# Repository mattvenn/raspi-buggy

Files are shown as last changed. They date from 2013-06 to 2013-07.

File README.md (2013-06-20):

# Raspberry pi scratch controlled drawing buggy

Simple buggy to control with scratch and python.

## Scratch 

A python listener is run on the raspberry pi which uses scratch's mesh networking capability to turn commands from scratch into motor controls.

Scratch itself is run on another computer to avoid the large overhead of sending graphics over the network.

## Python

The buggy can also be controlled direct from python.

# Build instructions

See the [instructions](docs/instructions.md) here.

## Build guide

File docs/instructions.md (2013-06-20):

# Buggy build instructions

# Get the parts

You will need:

*  some [male to male wires](http://oomlout.co.uk/products/jumper-wires-70-piece)
*  some [female to male wires](http://oomlout.co.uk/products/premium-female-to-female-jumper-wires-x21)
*  [l293d motor driver](http://oomlout.co.uk/products/motor-controller-l293d)
*  [400 point breadboard](http://oomlout.co.uk/collections/prototyping/products/breadboard-400-point)
*  4 AA battery holder and 4 *rechargable batteries* *TODO*
*  [buggy unit](http://www.mindsetsonline.co.uk/product_info.php?cPath=17_134_685&products_id=1034)
*  pen and bluetack if you want to do some drawing.

# Tools required

* flat screwdriver
* pliers
* soldering iron? *TODO*

# Build the buggy

Follow the instructions that came with the buggy, but don't put the wires through the central hole. Also, don't connect the switches to the motors. We'll use the l293d chip to control the motors instead.

# Build the circuit

Follow this diagram to build the circuit, but don't insert the batteries yet. The most important parts to get right are:

*  The black and red connections from the battery holder need to be the right way round.
*  The l293d chip needs to be the right way round - the little notch should be on the right.

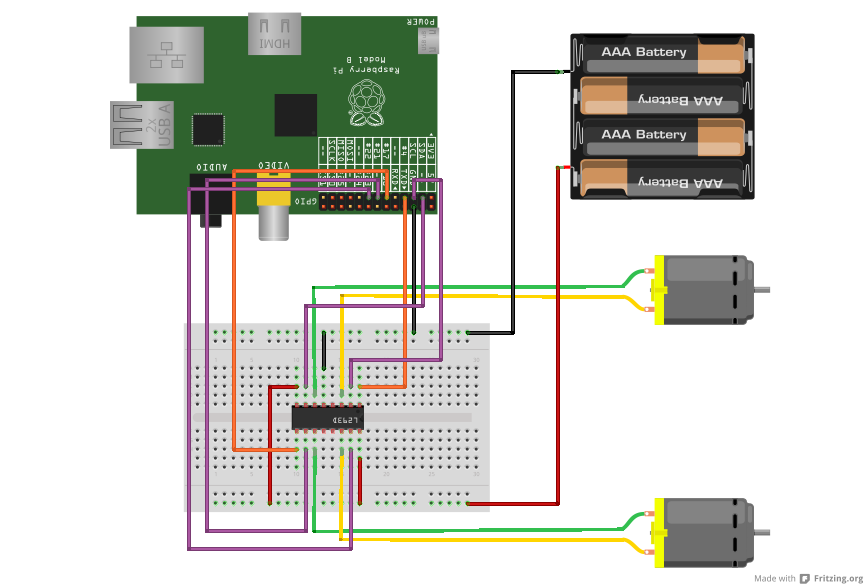
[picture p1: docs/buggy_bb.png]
circuit


The l293d is the chip that amplifies the small current from the raspberry pi to the larger current we need to drive the motors. It also lets us drive the motors forwards and backwards. You can learn more about the [l293d here.](http://www.ti.com/lit/ds/symlink/l293d.pdf)

# Setup the software on the Raspberry pi

## Log in to the raspberry pi

*TODO*
You will need to power up the raspberry pi and connect to it over the network.

## Download the buggy software

On the raspberry pi, start a terminal. Then run these commands to download the software:

    wget https://github.com/mattvenn/raspi-buggy/archive/master.zip
    unzip master.zip

Then we need to install some extra software for the buggy software to work.

## easy_install

easy_install makes it easier to install python libraries.

    sudo apt-get -y install python-setuptools

## RPIO

RPIO is the library that lets a python program control the raspberry pi GPIO pins - which we'll use to drive the motor chip.

    sudo easy_install RPIO

## scratchpy

scratchpy is the library we'll use to talk to scratch

    sudo easy_install scratchpy

## Test the motors

Change into the buggy directory:

    cd buggy-master

Then start the test running by running this command:

    sudo python buggy_demo.py

If all is well, the program will start printing lines like this:

    Using hardware: PWM
    PW increments:  10us
    stop
    0 of 10
    straight
    left forward pwm: 570
    right forward pwm: 570
    stop
    pause

If you don't see the above then you probably have missed out [installing one of the libraries](#download-the-buggy-software)

You can then connect the batteries, and providing your circuit is correct the buggy should start moving its motors!

The test will run 10 times, to stop the test early, you can press control-C

You can look at what the test does by using an editor:

    nano buggy_demo.py

It drives the motors in different directions to perform a sequence of moves: a straight line, a turn and then an arc. This is done 10 times. You can learn more about how the program works by reading [buggy.py](#buggy.py)

# Scratch

To use scratch to control the buggy, we run scratch on a different computer, and then send commands from scratch to the raspberry pi. To do that we need to use scratch's mesh function, which allows scratch to talk over the network to the raspberry pi.

The reason why we don't run scratch on the pi and then connect via [VNC](http://en.wikipedia.org/wiki/Virtual_Network_Computing) is that we've found it's too slow and annoying for children (and adults!) to use. We could connect a keyboard, mouse and screen to the raspberry pi, but then the robot wouldn't be very free to drive around.

## Configure scratch for mesh

Follow the [instructions here](http://wiki.scratch.mit.edu/wiki/Mesh#Mesh_by_Modification_of_Scratch) to enable mesh on scratch. 

Then [host Mesh](http://wiki.scratch.mit.edu/wiki/Mesh#How_to_Host_and_Join_Mesh_sessions). 

## Start Raspberry pi listening to scratch

We run the scratch_listener.py program on the raspberry pi to listen to the command from scratch. To do that, we need the IP address of the computer running scratch. [Follow these instructions to find your IP address.](http://computer.howstuffworks.com/internet/basics/how-to-find-ip-address.htm)

Then start the scratch_listener program like this (change IP_ADDRESS to your IP address)

    sudo python scratch_listener.py IP_ADDRESS

You should see this:

    Using hardware: PWM
    PW increments:  10us
    trying to connect to IP_ADDRESS : 42001
    connected

If you see this:

    Using hardware: PWM
    PW increments:  10us
    couldn't connect - is scratch running?
    [Errno 111] Connection refused

Then either scratch isn't setup for mesh networking, the mesh network isn't enabled, or you have the wrong IP address.

## Test the scratch connection

Download [the example buggy.sb scratch program](https://github.com/mattvenn/raspi-buggy/blob/master/buggy.sb?raw=true). And then load it in scratch.

Try pressing the arrow keys on your keyboard. Each arrow key should move a motor in one direction. You can press 2 buttons at once to use both motors. Now you can write your own scratch programs to draw some fun patterns!

# Controlling the buggy with Python

Controlling the buggy with python is easy. Log in to the raspberry pi and change to the buggy directory:

    cd buggy-master

Then have a look at the buggy_demo.py program. You can copy this program and change what happens. Then try out your changes by running the program again:

    sudo python buggy_demo.py

## buggy.py

buggy.py is a little library that sets up the GPIO pins and defines 2 functions that allow easy control of the motors. The first is called:

    buggy.drive(wheel,speed)

It takes 2 arguments, the wheel to control, and the speed to move the wheel at. The wheel is chosen by passing either buggy.LEFT or buggy.RIGHT. The speed can be set to -100 to +100. A speed of 0 will stop the motor. 

The second is used to stop both motors:

    buggy.stop_all()

To find out more about RPIO and how PWM works to control the motors at different speeds, you can read the [documentation here.](http://pythonhosted.org/RPIO/)

# Photos

Some [photos of the buggy and the pictures that it has drawn.](http://www.flickr.com/photos/matthewvenn/sets/72157633441674047/with/9027093148/)

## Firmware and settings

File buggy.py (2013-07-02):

#import the library to control the GPIO pins
import RPIO
from RPIO import PWM
RPIO.setwarnings(False)
import sys

PWM.setup()

#get rid of debug output
PWM.set_loglevel(PWM.LOG_LEVEL_ERRORS)

#import the time library
import time

#pins
#i2c pins can be enabled high at boot - see http://www.raspberrypi.org/phpBB3/viewtopic.php?f=44&t=35321
l_enable_pin = 4
l_forward_pin = 3
l_backward_pin = 2
r_enable_pin = 17
r_forward_pin = 27
r_backward_pin = 22

#constants
LEFT = 1
RIGHT = 2

#setup the pins
RPIO.setup(l_forward_pin, RPIO.OUT)
RPIO.setup(r_forward_pin, RPIO.OUT)
RPIO.setup(l_backward_pin, RPIO.OUT)
RPIO.setup(r_backward_pin, RPIO.OUT)

#pwm setup
dma_l = 0
dma_r = 1
PWM.init_channel(dma_l)
PWM.init_channel(dma_r)
#this is silly, but otherwise pwm will complain if we try and clear a channel that hasn't been already used
PWM.add_channel_pulse(dma_l,l_enable_pin,0,0)
PWM.add_channel_pulse(dma_r,r_enable_pin,0,0)

def stop_all():
    print "stop"
    PWM.clear_channel_gpio(dma_l, l_enable_pin)
    PWM.clear_channel_gpio(dma_r, r_enable_pin)

#direction, how long to drive for, how fast to drive
def drive(wheel,speed):
    if wheel == LEFT:
        print "left",
        dma = dma_l
        enable_pin = l_enable_pin
        forward_pin = l_forward_pin
        backward_pin = l_backward_pin
    elif wheel == RIGHT:
        print "right",
        dma = dma_r
        enable_pin = r_enable_pin
        forward_pin = r_forward_pin
        backward_pin = r_backward_pin
    else:
        error_msg( "unknown wheel")
        return


    if speed > 100 or speed < -100:
        error_msg("speed should be > -100 and < 100")
        return

    if speed > 0:
        RPIO.output(forward_pin, True)
        RPIO.output(backward_pin, False)
        print "forward",
    elif speed < 0:
        RPIO.output(forward_pin, False)
        RPIO.output(backward_pin, True)
        print "backward",
    else:
        print "stop",

    pwm_amount = int(abs(speed * (1999/100)))

    print "pwm:", pwm_amount
    PWM.add_channel_pulse(dma,enable_pin,0,pwm_amount)

def end():
    PWM.cleanup()

def error_msg(msg):
    sys.stderr.write(msg + "\n")

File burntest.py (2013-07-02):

import buggy
import time
import sys

"""
little demo to show buggy control via python
"""

buggy.stop_all()
max_speed = 60 
if len(sys.argv)==2:
    max_speed = int(sys.argv[1])
    print "maxspeed:", max_speed

pause_time = 1 #second
drive_time = 1 #second

while True:

    #straight line
    print "straight"
    buggy.drive(buggy.LEFT,max_speed)
    buggy.drive(buggy.RIGHT,max_speed)
    time.sleep(drive_time)
    buggy.stop_all()

    print "pause"
    time.sleep(pause_time)

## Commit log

2013-06-12 added direction and both wheels, but seem to have broken scratch comms
    [buggy.py, scratch_listener.py]
2013-06-12 tested working on left wheel, dont have wires to test right atm
2013-06-20 added some documentation
    [buggy.fzz]
2013-06-22 changed enable pin away from i2c to avoid motor running at boot
    [buggy.py]
2013-06-22 updated docs to reflect gpio pin change
    [buggy.fzz]
2013-06-22 pic was not sized properly
    [buggy.fzz]
2013-06-22 changed max speed for lower voltage battery
2013-06-24 burntest for testing batteries
    [burntest.py]
